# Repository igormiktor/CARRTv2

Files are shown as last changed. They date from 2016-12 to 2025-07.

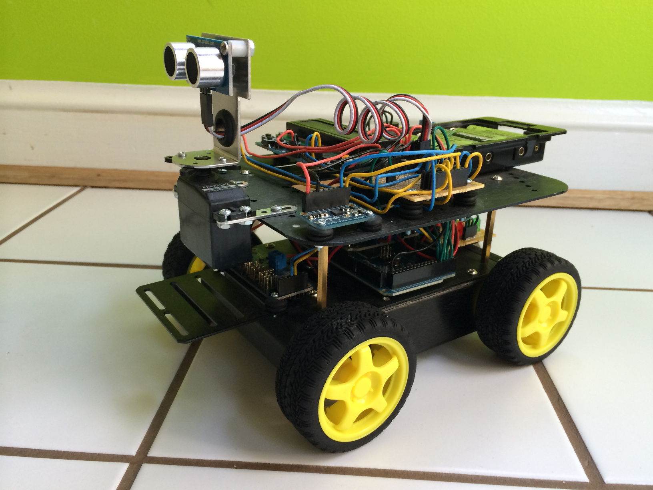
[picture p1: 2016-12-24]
images/CARRT_01.jpg

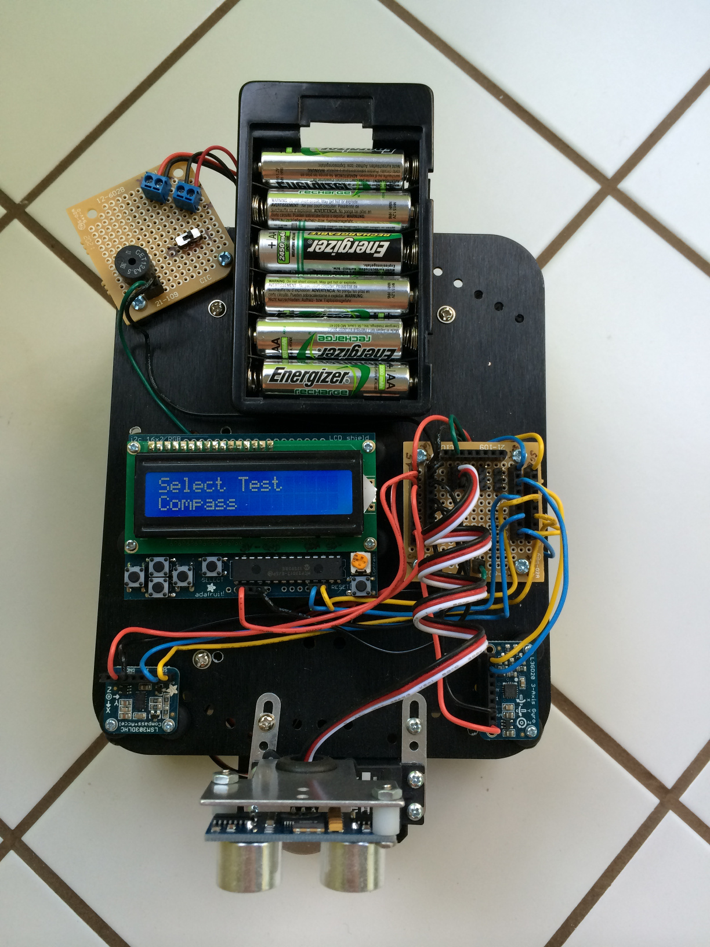
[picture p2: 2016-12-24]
images/CARRT_04.jpg

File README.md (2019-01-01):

# CARRTv2
Cute Autonomous Robot Rover Thing (version 2)

Goal of this project is to create a small robotic vehicle (CARRT) that can do the following:

- Start in one room of the house;
- Receive a goal position, specified relative to its starting location (e.g., 8 meters North, 4.5 meters West);
- Autonomously make its way to the new position, mapping doors and walls with its ultrasonic radar until it finds a path to the goal;
- Build a map as it goes, enabling effective back-tracking whenever it hits a dead-end.

This is both a hardware and a software project.

The hardware consists of a four-wheeled chassis carrying an ArduinoMega 256 and an Adafruit motor driver board.  Navigation is
enabled by an LSM303DLHC three-axis accelerometer and magnetometer and an L3GD20 three-axis gryoscope.  A Garmin Lidar Lite
sensor mounted on a servo allows CARRT to sense obstacles (both furniture and walls) and navigate around them.

The hardware and how it is wired together is described in the `schematics` sub-directory by a
[Fritzing](http://fritzing.org/home/) project file.
Photos of CARRT appear in the `images` sub-director and on the project wiki.

The software is found in the `source` directory.  Having the entire software
system fit and operate within the constraints of the ArduinoMega 256 (8 bit, 16
MHz ATmega 2560 microcontroller; 8 KB SRAM; 256 KB program memory) is the
primary challenge.  The rather low precision of the LSM303DLHC and the L3GD20 as
well as the poor reliability of a magnetometer operating inside a house (bring
up the compass on an iPhone, set the iPhone on the floor and just watch as you push
the iPhone slowly past an operating refrigerator) make indoor navigation the
secondary challenge.

The name "CARRT" is thanks to my daughter.

## Specs

* Main microcontroller
    * Arduino Mega256 board
    * CPU: ATmega2560 8-bit, 16MHz microcontroller
    * 256KB flash memory (program memory)
    * 8KB SRAM (working memory)
    * 4KB EEPROM (permanent memory)
* Power buses
    * Two power buses
    * First power bus supplies the Arduino Mega256
        * Arduino in turn supplies regulated 5V power to all other ICs
    * Second power bus supplies unregulated power to motors and servos
* Motor controllers
    * L293D H-Bridge ICs to control 4 DC motors
    * Total of 4 L293Ds are used
    * L293Ds control the unregulated motor power bus
    * L293Ds stacked in pairs to support 1.2A sustained current to DC motors
    * SN74H595 shift-register IC is used to control the L293Ds
    * SN74H595 works off the regulated 5V power bus
* 2 x 16 character LCD display
    * LCD controlled by an HD44780U
    * MCP23017 drives the HD44780U
* LSM303DLHC triple-axis accelerometer and magnetometer
* L3GD20 triple-axis gyroscope
* PCA9685 16-channel PWM/Servo driver
    * Used to drive the Parallax servo
* Parallax 900.00008 servo
* Garmin Lidar Lite v3
    * Mounted on the Parallax servo
* PING))) ultrasonic distance sensor
    * Used for obstacle detection while moving
* TMP36 analog temperature sensor
* PS1240 piezoelectric buzzer

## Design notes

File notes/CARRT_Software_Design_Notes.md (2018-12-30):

# CARRT Software Design Notes

## Design Principles

This version of the software is based on the following design principles:

1. **Highly modular and decoupled.** Compartment details as much as
possible; present only the higher level interfaces needed by other
components, and no more.

2. **Separate low-level hardware interfaces from higher-level code.** Software
drivers are provided for all the hardware sub-systems, even trivial hardware
such as the piezo-electric buzzer. In keeping with principle #1, all details of
the hardware are encapsulated by the drivers.

3. **Prefer functional interfaces to object interfaces.** All the
hardware on CARRT is "one of".  This is true even for the four drive
motors because they are all controlled through a single SN74H595 and so behave
as a single hardware subsystem.  If hardware drivers are presented as
objects, then the code has to manage a singleton object and make it
visible to code that needs to access it.  Functional interfaces are
easier and cleaner in this case, and avoid the proliferation of global
objects or the overhead of singleton classes to manage them.

4. **Use namespaces to compartmentalize modules.** Namespaces serve to
prevent name clashes and bind the functions that belong together
logically, much like using static class members. They also expose a
simplified interface in header files, as compared to classes with static members.

5. **Represent CARRT higher-level functions as an event-driven state
machine.**   Whatever CARRT is doing is represented as a state.
Changes in behavior are changes in state. States are narrowly
defined and simple.  More complex behaviors are decomposed into
simpler actions that correspond to simple, easily defined states.

6. **Represent states by classes.**  In this case, objects are the natural and
appropriate way to implement states.  Objects that inherit from a base class
allow simple and consistent management of states and a seamless process for
switching between states.

7. **States, and only states, are created dynamically.**  It may seem crazy
to use dynamic memory allocation on a microcontroller, but this principle is
based on actual testing that showed dynamic allocation offered the best
tradeoff.  If states are not allocated dynamically, then all states have to be
allocated globally, which consumes a very significant amount of SRAM (states are
generally small, but there are many of them).  Because only one state is active
at a time, and no more than two are ever "alive" simultaneously (when states are
changing, both the outgoing and incoming states are briefly alive at the same
time), allocating states dynamically offers a significant reduction in
memory used at any instant in time.  Further supporting the use of dynamic
memory allocation for states are the following considerations:
    * The avr-libc implementations of `malloc()` and `free()` (upon
    which `new` and `delete` are implemented) are efficient and
    relatively fast.  And `free()` is pretty good at minimizing heap
    fragmentation.
    * The pattern of how states are allocated and released (create a new
    state; delete the old one; repeat) combined with the generally small
    size of states limits the fragmentation of the heap to at most a
    free block the size of the largest state.  And even that fragment will be
    reclaimed on the very next state change because a new smaller state
    will then be created at the bottom of the heap (where the free
    fragment is) and then all the memory above it will be recombined
    into an un-fragmented free block when the old state (the state that
    had fragmented the heap) is released.

8. **Navigation is provided as a separate, stand-alone service.** The
Navigator is in essence a higher-level "driver" that is implemented on top of
the lower-level hardware drivers.

9. **All strings are placed in PROGMEM (flash memory).**  SRAM is
precious.  Because strings are needed only to support the user interface,
string operations are never time critical.  While putting strings
in PROGMEM makes access much slower, the slower access doesn't matter
and the reduced SRAM usage is really important.

10. **Support selective compilation of major elements.**  CARRT is constrained
by SRAM. While it is useful to have a full set of testing code, it invariably
uses up precious SRAM.  So it is important to build the code in a way that
testing code (or any other major elements of CARRT, such as the "programmed drive"
feature) can be omitted at compile time while still building a CARRT executable
that is otherwise fully operational apart from the omitted functionality

## History and Lessons

The initial implementation of CARRT software was developed in parallel with the
hardware build. There were many lesson learned on both sides. For example, the
original hardware had only a single power bus for both the motors and the
electronic components.  Initial testing showed this to be a bad design: when the
motors turned on they caused large voltage drops that then triggered a reset in
the ATmega 2560. That's why now there are two separate power buses, one for motors
and one for ICs. Another example is that trying to drive a servo directly from
the ATmega 2560 using PWM caused servo jitter due to the many other interrupts
that the ATmega 2560 had to service.  This is why CARRT now uses a dedicated PCA9685
board to control the servo.

The initial software also avoided use of dynamic memory allocation: all
states were pre-allocated as global objects.  As the number of states grew, this
quickly consumed much of available SRAM.  This was further exacerbated by
numerous user-interface strings that were stored in SRAM.  Each behavior (i.e.,
state) added to CARRT further exacerbated the problem.

Implementing software interfaces to hardware as objects created a
significant number of global objects that had to be managed and shared.
Eventually, this became a header file full of `extern` declarations of
global objects, which in turn had to include headers defining each of
these objects.  This became a headache to manage, slowed compilation,
and had the effect of making everything dependent on everything.

Additionally, some of the software interfaces were initially coded at the
wrong level of abstraction (generally too low a level).  This resulted in
what effectively became multiple layers of drivers (each somewhat higher
level) for a single (simple) piece of hardware.  This was needlessly
inefficient and hard to understand and debug.

Finally, the parallel development of hardware and software not only resulted in
a somewhat ad-hoc development of code, but also led to
undesirable coupling of testing code and operational code in some places and
code duplication in others.  This was inherently inefficient and as well as hard to
adapt and maintain when new hardware was added and/or changes were need.

All these lessons (and numerous smaller ones) have been incorporated
into version 2 of the CARRT software.

## Implementation Overview

The implementation is at its core an event-driven state machine: the heart of
CARRT is an event loop that takes incoming events, feeds them to the current
state, which in turn takes appropriate actions (including triggering a change to
a new state).

The top level view of current CARRT implementation is as
follows:

* Initialization.  Configure the microcontroller appropriately, initialize all
hardware subsystems, initialize the state machine, and start internal timers.

* Event loop. This is the heart of CARRT.  The main loop is very simple: pull
the next event from the event queue, handle any system-level events (navigation
updates, errors, resets, etc), pass any other events to the current state (this
is where all the behaviors happen), and then (when the state is done with the
event) optionally perform (non-essential) housekeeping tasks.

* Reset. If a reset is requested, ensure everything is shutdown appropriately,
clean up, and then go back to initialization.

Initialization and reset are handled in CarrtMain.cpp; the event loop is managed
in MainProcess.cpp.  State behavior is defined by the State class (State.h
and State.cpp).  States have a simple interface of three member functions:
onEntry(), onEvent(), and onExit().  When a state becomes active (i.e.,
current), but before any events are processed, MainProcess will call the state's
onEntry() function.  This provides a mechanism for the state to initialize or
otherwise prepare itself.  The MainProcess will then repeatedly pass events to
the state's onEvent() function.  It will continue to do so until there is a
change of state (usually, but not always, initiated by the current state's onEvent()
function).  When a change of state is triggered, the MainProcess will then call
the current (about to depart) state's onExit() function, allowing the state to perform whatever clean
up is appropriate.  In most cases, the last thing the state's onExit() will do
is delete itself: this is the default action of State::onExit(). In some
situations (e.g, for states that are part of a user-entered program of actions
which the user may replay repeatedly) states will override the self-delete
behavior in onExit().  After calling the departing State's onExit(), MainProcess will
then call the incoming State's onEntry() function.

Events are defined and managed by the EventManager (EventManager.h,
EventManager.cpp).  At this time, events consist of timer-related events,
navigation-related events, keypad-related events, and error events.  The
timer-related events are the most important, as they provide the heart-beat that
enables States to preform a variety of actions, such as monitoring drive
progress or navigation parameters, updating displays, tracking elapsed time, and
initiating time-related actions.  Timer-related events are generated by the
EventClock (EventClock.h and EventClock.cpp), which relies on one of the ATmega
2560's hardware timers to trigger interrupts that are used to queue
timer-events. Note also that changes of state are not events, but rather
something that happens as a result of an event.

The inertial navigator (Navigator.h and Navigator.cpp) is implemented as an
independent module that effectively runs in the background.  The MainProcess
feeds it dedicated navigation update events every eighth of a second, which the
Navigator uses to read accelerometer, magnetometer, and gyroscope data and update
its internal navigation state.  At any time, States can call appropriate
Navigator functions to obtain the current position, direction, and velocity.  To
help the Navigator out, States inform the Navigator about what CARRT is doing
(e.g., driving straight, turning, stopped, etc) by calling appropriate Navigator
functions (e.g., Navigator::movingStraight(), Navigator::movingTurning(),
Navigator::stopped(), etc).

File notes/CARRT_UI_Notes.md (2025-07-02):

# CARRT User Interface Overview

## Keypad
```
+-----------------------------------------+
| +-------------------------------------+ |
| |                 LCD                 | |
| +-------------------------------------+ |
|        1                                |
|     2     3    5   <--- Keypad Buttons  |
|        4                                |
+-----------------------------------------+
```

The diagram above identifies the buttons on the LCD keypad.  These are
referred to as follows:

* button 1 = UP
* button 2 = LEFT
* button 3 = RIGHT
* button 4 = DOWN
* button 5 = SELECT

It is also possible to enter simultaneous combinations of buttons, referred to as "chords".
Several chords have unchanging meaning.  These chords are:

* button 3 & button 5 = RIGHT & SELECT = RESET
* button 2 & button 3 = LEFT & RIGHT  = PAUSE
* button 1 & button 4 = UP & DOWN     = CONTINUE

* RESET always performs a full soft reset of CARRT.  All systems and sub-systems are
completely reinitialized.  It is effectively equivalent to cycling the power.

* PAUSE suspends the current activity in the sense that no further
state-level event processing (and therefore no further state-level
actions) will occur.  Note that "pause" can in some cases be
counterintuitive:  pausing a "forward drive" state while it is driving
will effectively cause CARRT to continue to drive indefinitely: the
events that trigger driving to stop will not be processed.

* CONTINUE will "undo" a PAUSE, allowing the active state to continue
processing events and taking corresponding action.  Note that "continue"
can in some cases be counterintuitive:  continuing a paused "forward
drive" state while it is driving will may not cause it to stop: if the
events that trigger driving to stop have already gone by, then the state
will never see them and will therefore not stop.

Apart from the above chords, the meaning of the buttons varies with menu items,
although the operation is generally intuitive.  The precise meanings, especially
any that are not perhaps intuitive, are described in the appropriate menu
sections.

## Menus

The menu system has a consistent user interface:  the UP and RIGHT buttons move
to the next menu item; the DOWN and LEFT buttons move to the previous menu item;
the SELECT button selects that menu item.

The remaining sub-sections walk through the menu options

### Welcome to CARRT (top-level menu)

This is the top-most menu in CARRT.  It presents four menu options:

* **Run Tests...** Leads to a menu of test options.

* **Prgm Drive...** Leads to menus that allow users to program a drive and run
it.

* **GoTo Drive...** Leads to menus that allow users to enter a destination and
have CARRT go to it.

* **Nav Info...** Displays CARRT's current position (relative to the
original starting position) and the current heading.

* **About...** Leads to menus that display information about CARRT's firmware.

Note that the first three options are present only if they are selected at
compile time.

### Run Tests... (second-level menu)

This menu presents a series of tests.  Selecting one of them runs the corresponding test.
The options under this menu are:

* **Exit...**  Returns to the top-level menu

* **Memory** Displays memory information.  The UP and DOWN buttons toggle
between displaying total free SRAM and total used SRAM. The LEFT and RIGHT
buttons toggle between displaying total SRAM and displaying the SRAM between the
stack and the heap (the "free stack" space).  The SELECT button returns to the **Run
Tests...** menu.

* **1/4 Sec Events**  Counts 1/4 second events.  Continues until any button is
pressed, which returns to the **Run Tests...** menu.

* **1 Sec Events**  Counts 1 second events.  Continues until any button is
pressed, which returns to the **Run Tests...** menu.

* **8 Sec Events**  Counts 8 second events.  Continues until any button is
pressed, which returns to the **Run Tests...** menu.

* **Beep**  Makes beep sounds until any button is pressed, which returns to the
**Run Tests...** menu.

* **Temp Sensor**  Displays the temperature as measured by the TMP36 analog
temperature sensor, updated every second.  Pressing any of the UP, DOWN, LEFT,
or RIGHT buttons toggles the display between degrees F and C.    The SELECT
button returns to the **Run Tests...** menu.

* **Batt LEDs**  Cycles through the battery level LEDs.  Continues until any
button is pressed, which returns to the **Run Tests...** menu.

* **Motor Batt**  Displays the voltage of the batteries that power the motors
and servos, updated every second.    Continues until any button is pressed,
which returns to the **Run Tests...** menu.

* **CPU Batt**    Displays the voltage of the batteries that power the electronic
components, updated every second.    Continues until any button is pressed,
which returns to the **Run Tests...** menu.

* **Sonar**  One a second the sonar measures and displays the range to whatever
is in front of it.  Continues until any button is pressed, which returns to the
**Run Tests...** menu.

* **Lidar**  The lidar slews to straight ahead, makes a range measurement, and
displays it.  Pressing the LEFT or RIGHT buttons slews the lidar accordingly.
Pressing the UP or DOWN button triggers a new lidar range measurement at the
current slew angle.  The SELECT button returns to the **Run Tests...** menu..

* **Range Scan**  The lidar performs a scan from right to left (covering a 120
degree arc), measuring and displaying the range to the nearest obstacle at 10
degree increments.  Every 4 seconds, the lidar slews 10 degrees to the new
bearing angle and displays the range to the nearest obstacle.  Continues until
any button is pressed, which returns to the **Run Tests...** menu.

* **Compass**  Displays the compass bearing in degrees, updated every
second.  Continues until any button is pressed, which returns to the
**Run Tests...** menu.

* **Accelerometer**  Displays the accelerometer readings in Gs, updated every
second.  The LEFT and RIGHT buttons cycle the display through the x-, y-, and
z-axes.  The UP and DOWN buttons toggle the display between raw accelerometer
readings and nulled accelerometer readings (nulled means the average at-rest
accelerometer reading is subtracted out).  The intent is that you can observe
the readings as CARRT is manually moved around.  The SELECT button returns to
the **Run Tests...** menu.

* **Gyroscope**  Displays the gyroscope readings in deg/sec, updated every
second.  The LEFT and RIGHT buttons cycle the display through the x-, y-, and
z-axes. The UP and DOWN buttons toggle the display between raw gyroscope
readings and nulled gyroscope readings (nulled means the average at-rest
gyroscope reading is subtracted out).  The intent is that you can observe the
readings as CARRT is manually spun around.  The SELECT button returns to the
**Run Tests...** menu.

* **Drive Fwd/Rev**  Repeatedly drives forward for a second, pauses for a
second, drives backward for a second, and pauses for a second.  Continues until
any button is pressed, which returns to the **Run Tests...** menu.

* **Drive Left/Right**  Repeatedly rotates left for a second, pauses for a
second, rotates right for a second, and pauses for a second.  Continues until
any button is pressed, which returns to the **Run Tests...** menu.

* **Nav. Rotation**  Engages the Navigator and displays which direction CARRT
believes it is pointed in (according to both compass and Navigator), updated
every second.  Continues until any button is pressed, which returns to
the **Run Tests...** menu.  The intent is that CARRT will be place on a
lazy-susan and spun around to check the performance of the Navigator.

* **Nav. Drive**  Engages the Navigator, drives forward for 5 seconds, and then
pauses to display how far (in cm) CARRT's Navigator believes it has traveled from
its starting point.  When any of the LEFT, RIGHT, UP, or DOWN buttons is pressed,
CARRT drives in reverse for 5 seconds, and again pauses to display how far CARRT's
Navigator thinks it is from its original starting point.  This continues until the
SELECT button returns to the **Run Tests...** menu. This allows checking CARRT's
internal estimates of distance traveled against actual measurements.

* **Error Handling**  Displays a short count-down and then triggers a error
condition, which (should) lead to the display of an error message (error code
601). The only recovery options are to perform a soft reset by simultaneously pressing
the RIGHT and SELECT buttons, or cycling the power.

### Prgm Drive... (second-level menu)

This set of menus allows the user to select from a set of actions and add them
to list of programmed CARRT actions.  Users can also clear the list or run the
list of actions (a "programmed drive").  The list is remembered (even if the
user exits the **Prgm Drive...** menu) until it is explicitly cleared.  The
number on the right
side of the top-row of the LED display shows the number of actions in the
currently stored "programmed drive".

The options under this menu are:

* **Exit...**  Returns to the top-level menu (the list of actions is
remembered).

* **Go Fwd Time**  Go forward for a user-specified number of seconds.

* **Go Fwd Dist**  Go forward for a user-specified distance in cm.

* **Go Rev Time**  Go in reverse for a user-specified number of seconds.

* **Go Rev Dist**  Go in reverse for a user-specified distance in cm.

* **Rotate L Time**  Rotate left (counter-clockwise) for a user-specified number
of seconds.

* **Rotate R Time**  Rotate right (clockwise) for a user-specified number of
seconds.

* **Rotate Angle**  Rotate a user-specified angle in degrees.  Negative angles
are to the right (clockwise); positive angles are to the left
(counter-clockwise).

* **Pause**  Pause (do nothing) for a user-specified number of seconds.

* **Beep**  Beep for a user-specified number of seconds.

* **Scan**  Conduct a range scan from -60 degrees relative to 60 degrees
relative, measuring and displaying the range to the nearest obstacle every 10
degrees.

* **Run it...**  Run the "programmed drive" using the currently stored actions.

* **Clear...**  Erase the currently stored actions.

### GoTo Drive... (second-level menu)

This set of menus allows the user to set a Go-To point and have CARRT
then autonomously drive to that Go-To point.  The Go-To point can be entered
either relative to CARRT's current orientation and position or in absolute
North and East coordinates measured from CARRT's current position.

The options under this menu are:

* **Relative Goto...**  Specify a Go-To point relative to CARRT's current
orientation and position.  A series of prompts will allow the user to enter
the Go-To point as cross-range and down-range in centimeters (cm) from CARRT.
Forward (downrange) and left/counter-clockwise (crossrange) are positive;
backward and right/clockwise are negative.

* **N & W Goto...**  Specify a Go-To point in North and West coordinates
measured from CARRT's current position.  A series of prompts will allow the
user to enter the Go-To point as distance (cm) to the North and West of CARRT.
South and East are entered as negative values.

* **Exit...**  Returns to the top-level menu.

### Nav Info... (second-level menu)

This menu displays the current position in centimeters North and West of the
original starting position, as well as the current heading (direction CARRT
is pointed towards) in degrees.  This is static information that is not
updated if CARRT is manually moved while the information displays.

Pressing any button returns to the top-level menu.

### About... (second-level menu)

This menu displays a series of information about CARRT's current firmware. The
UP and RIGHT buttons move to the next display; the DOWN and LEFT buttons move
to the previous display.  The SELECT button returns to the top-level menu.
The display options are:

* **Version**  Displays the version number of the software and the features
included in the firmware.  The feature codes are:
    * **T**  Firmware includes Tests
    * **P**  Firmware includes Programmed Drive
    * **G**  Firmware includes GoTo Drive
    * **IMU**  Firmware uses inertial navigation
    * **DR**  Firmware uses dead-reckoning navigation
    * **D**  Firmware includes debugging output using Serial0

* **Build Date**  Displays the date and time the firmware was built.

* **Git SHA1**  Displays the SHA1 of the git HEAD from which the firmware was
built. This is useful for recreating the exact firmware currently loaded on
CARRT.

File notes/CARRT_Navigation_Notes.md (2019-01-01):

# CARRT Navigation Notes

## Overview

CARRT can be compiled with one of two different navigation modes. The first mode
is inertial navigation. It uses the accelerometer, magnetometer and gyroscope as
an inertial measurement unit, estimating distance moved by (double)
integration of the acceleration.  The second mode is dead reckoning.  This mode
uses the accelerometer, magnetometer, and gyroscope for orientation only,
and estimates distance moved using an empirically-derived formula that
converts time spent moving into distance moved.  The mode is chosen at compile time by
#defining either CARRT_NAVIGATE_USING_INERTIAL or
CARRT_NAVIGATE_USING_DEADRECKONING.

## Common to both Navigation Modes

The overall approach to navigation, the underlying choices of coordinate systems, and the implementation of
these fundamental elements are common to both navigation modes.  These common elements are:

* Coordinate system: The global coordinate system used by CARRT for navigation places North along the
positive X-axis and West along the positive Y-axis.  This allows the 0 direction to map to North and
enables the standard conversions between Cartesian (x,y) coordinates and Polar (r,&theta;) coordinates.
All navigation and navigation-related activities, such as mapping, are done in the global (N,W) coordinate
system.

* Local coordinates: The accelerometer and magnetometer both provide data in local, CARRT-centric,
3-D coordinates in which the X-axis points in CARRT's forward direction, the Y-axis points
to CARRT's left, and the Z-axis points upward.  The gyroscope provides angular rates along these same
three local axes. The conversion from local coordinates to global coordinates is dynamic, changing
over time as CARRT's orientation in 3-space changes (of course, orientation in the horizontal plane is
the primary consideration because CARRT usually doesn't drive on slopes&mdash;but the conversion
also works in that case).

* Angles: Navigation internally uses standard mathematical angles in radians, measured counter-clockwise
from the X-axis (North-axis). Conversion to compass angles is straightforward:

    compass = (360 - &theta; * 180 / pi) modulo 360

* Units: The units for the global (N,W) coordinates are internally maintained in meters (m).  Velocity is in
m/s, and acceleration is in m/s^2.  For convenience, centimeters (cm) units are commonly used in displays and
for keypad entry.

* Update rate: Navigation parameters are updated every 1/8 second.  The update reads all three instruments
(accelerometer, magnetometer, and gyroscope) and updates the orientation and position of CARRT.

Both navigation modes execute the following overall process:

1. Read the accelerometer, magnetometer, and gyroscope.

2. Estimate CARRT's current compass heading from the accelerometer and magnetometer data.  This step
also establishes the coordinate transformation between the local and global coordinate systems.

3. Estimate CARRT's current compass heading by integrating the gyroscope's angular rate data.

4. Combine the two compass estimates to get a "best" estimate for CARRT's current compass heading.

5. Using a velocity estimate (obtained differently for the different navigation modes), estimate
the distance traveled and update the global (N,W) coordinates of CARRT's current position.

The coordinate transformation figured out in step 2 is essential to all other
computations because all measurement data is in 3-D local coordinates but
must ultimately be converted to the 2-D global (N,W)
coordinate system. It isn't immediately obvious how to get to the global
coordinate system from the accelerometer, magnetometer, and gyroscope
measurements which are reported  as 3-D vectors in local coordinates.  The key to
converting from local to global coordinates is the observation that the cross
product of the magnetometer and the accelerometer output vectors gives an East
vector expressed in local coordinates.  The magnetometer output is a North
vector expressed in local coordinates, and these two vectors (East and North)
provide an orthogonal basis vector set for the global coordinate system expressed
in local coordinates.  With this basis set in hand, the local-to-global conversion
is straightforward.

## Inertial Navigation Mode

In inertial navigation mode the first 4 steps are executed as described above.
To implement step 5, the acceleration vector from the accelerometer is first
converted from local to global (N,W) coordinates. It is then integrated and
added to the velocity from the prior time-step to produce an estimate of the
current velocity vector.  A second integration is then performed on the current
velocity to get distance traveled and the result is added the position at the
prior time-step.  This generates an estimate of CARRT's current position.

The double integration required in inertial navigation mode is very sensitive
to errors in the acceleration measurement.  Several mechanism are used to help
limit those errors:

* To obtain the best acceleration measurement possible, each accelerometer "measurement" actually is an
average of 12 accelerometer measurements equally spaced in time over the previous 1/8 second.

* The measured acceleration is filtered to remove near-zero values. These small, near-zero accelerations are
replaced by 0 to ensure that "noise" isn't treated as actual acceleration (which if repeatedly integrated
can generate significant velocities).  The filter settings were determined empirically by analyzing the
noise in accelerometer measurements while CARRT was stationary.

* The estimated velocity obtained after integrating acceleration is constrained to what has been empirically
determined as CARRT's top speed.  This prevents the integration process from producing unreasonable velocities.

* When CARRT stops, velocity and acceleration are forced to 0 (regardless of what the accelerometer or other
instruments report).  And no navigation updates occur while CARRT is stopped.

Despite these steps, the velocity estimates occasionally spike high, maxing out velocity and excessively
over-estimating the distance traveled.  However, in most cases inertial navigation mode tends to underestimate
distance traveled.  The underestimate is generally 40% to 70% of actual distance traveled. The amount
underestimated cannot be reliably reproduced and seems to have a random component.  I have not been able to
determine the cause of these underestimates.  Nor, for that matter, have I been able to determine the cause of
the occasional velocity spikes.

For these reasons, I implemented an alternate navigation mode that implements dead-reckoning.

## Dead-Reckoning Navigation Mode

The implementation of dead-reckoning navigation mode follows the same first 4 steps, just like inertial
navigation mode.  This includes taking accelerometer measurements because the acceleration vector is needed
to compute heading and determine the conversion from local to global coordinates.  In dead-reckoning mode,
this is the only use of  acceleration data.

To compute distance traveled, dead-reckoning mode uses a simple linear model of distance traveled as a
function of time.  This model was derived from empirical measurements of how far CARRT traveled over time. The
data showed that a linear model was a surprisingly good fit. This linear model is documented and implemented
in DriveParam.cpp, which includes functions to compute both distance given time and time given distance.

So, at each 1/8 second update,  dead-reckoning navigation mode simply uses the linear model to
compute how far CARRT traveled during that 1/8 of a second and applies it along CARRT's current heading
vector to update the prior time-step position to the current position.

Dead-reckoning mode has some risks and error sources:

* Doesn't account for slippage or slowing due to obstacles (e.g., getting over the lip of a rug).

* Doesn't account for drive speed dropping as motor battery levels drop. However, limited experimentation
indicates that CARRT drive speed stays pretty constant until some point at which it drops significantly and
rapidly.  So this problem can be minimized by driving with batteries that are "not too low".

* The linear approximation error is highest for short (< ~2 sec) drives.  But even then the error in the linear
model is much less than the errors observed from inertial mode navigation.  Note that this applies to actual
drive times&mdash;not 1/8 second intervals of a longer drive.  Because of the linear model, adding up 1/8 second
intervals to compute distance traveled during a 30-second drive produces the same answer as computing the
distance traveled for a 30-second drive. The statement here applies to an actual drive: the estimate for a 30-second
drive (regardless of how it is computed) will be pretty accurate; the estimate for a 1/2 second drive (however computed)
will be much less accurate.

All-in-all, the dead-reckoning navigation model appears to work well enough for autonomous driving over the kinds
of distances and conditions encountered during "inside the house" driving that CARRT was designed for.

Nevertheless, it is frustrating that I couldn't get inertial navigation mode to work...

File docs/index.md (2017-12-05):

---
layout: home
#title: CARRT &mdash; an Autonomous Path-Finding Rover
#permalink: /
---

# CARRT v2

Goal of this project is to create a small robotic vehicle (CARRT) that can do the following:

- Start in one room of a house;
- Receive a goal position relative to its current position;
- Autonomously make its way to the goal position, mapping doors and walls with its lidar until it finds a path to the goal;
- Build a map as it goes, enabling effective back-tracking whenever it hits a dead-end.

And do it all based on an 8 bit, 16 MHz microcontroller with only 8 KB of SRAM...

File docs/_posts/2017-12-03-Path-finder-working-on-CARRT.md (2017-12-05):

---
layout: post
title:  "Pathfinder working on CARRT"
date:   2017-12-03 10:09:18 -0500
categories: CARRT update pathfinder
---

The pathfinder is now implemented and tested on CARRT itself.  The original pathfinding code was developed and tested on Linux.
It's now working on CARRT's 8-bit, AVR processor with only 8K of SRAM.

It's been tested both with "manually" entered maps (PathFindingBasicTest.cpp) and with lidar-generated maps (PathFindingTest.cpp).

Next task is to create the menus and states that actually execute the pathfinding and then drive the resulting path (re-mapping and
re-pathfinding as appropriate along the way).

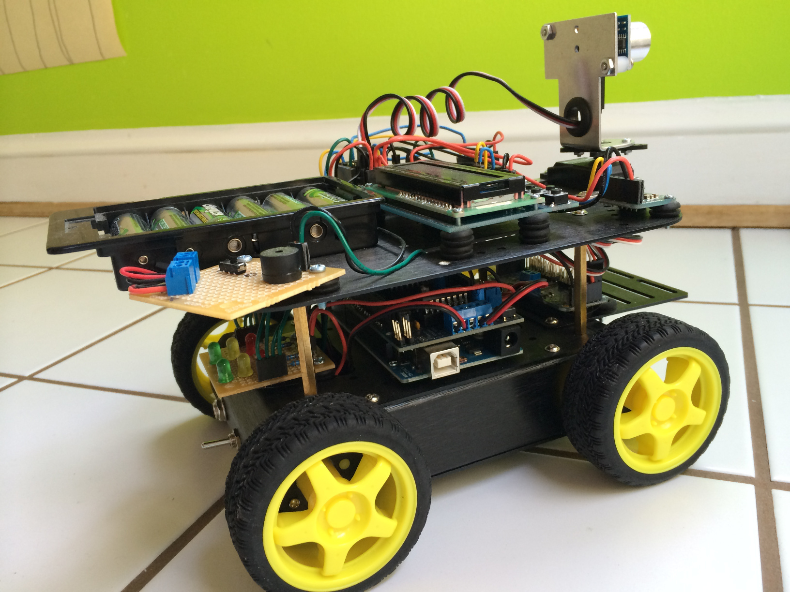
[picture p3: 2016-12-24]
images/CARRT_03.jpg

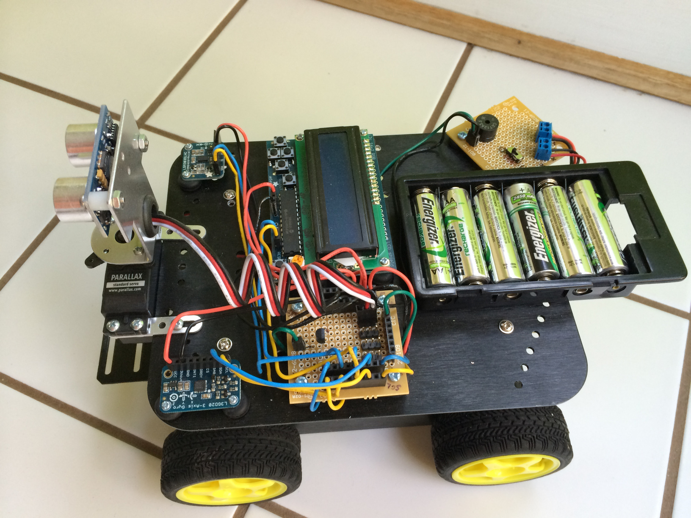
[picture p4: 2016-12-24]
images/CARRT_02.jpg

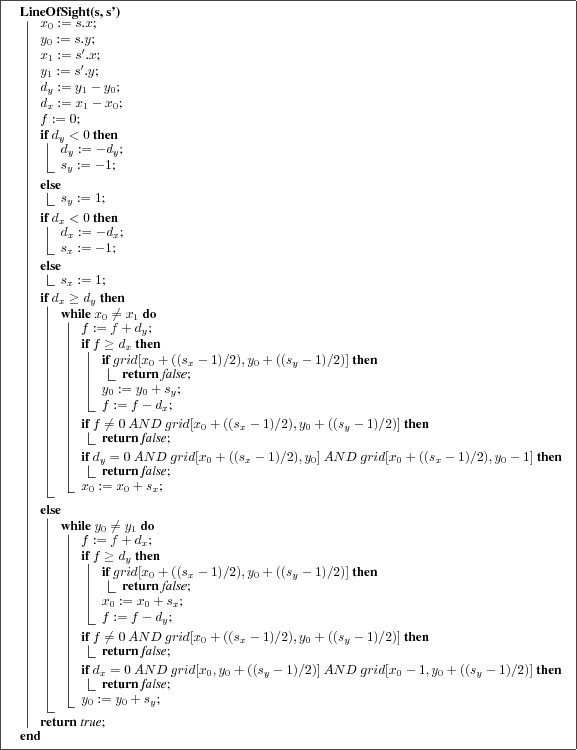
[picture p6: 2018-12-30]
notes/LoS.png

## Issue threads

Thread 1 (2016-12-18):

To do list

igormiktor, 2016-12-18:
Testing checklists

- [ ] Display driver
- [ ] Keyboard driver
- [ ] Navigator
- [ ] Map Keeper

igormiktor, 2017-01-07:
Notes fixes:

- [ ] Reset is right & select
- [ ] Four too level menu options
- [ ] The options are....
- [ ] free stack space
- [ ] covering a 120 degree arc
- [ ] compass updates every second
- [ ] intent of nav drive

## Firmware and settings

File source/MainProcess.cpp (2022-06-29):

/*
    MainProcess.cpp - Functions that run CARRT's main process which manages
    CARRT's states

    Copyright (c) 2022 Igor Mikolic-Torreira.  All right reserved.

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
    You should have received a copy of the GNU General Public License
    along with this program.  If not, see <http://www.gnu.org/licenses/>.
*/




#include "MainProcess.h"

#include "AVRTools/SystemClock.h"
#include "AVRTools/MemUtils.h"

#include "ErrorCodes.h"
#include "ErrorState.h"
#include "EventManager.h"
#include "Navigator.h"
#include "State.h"
#include "WelcomeMenuStates.h"

#include "Drivers/Battery.h"
#include "Drivers/Keypad.h"
#include "Drivers/Motors.h"

#include "Utils/DebuggingMacros.h"


#if CARRT_ENABLE_DEBUG_SERIAL

#include "BuildInfo.h"

namespace
{
    const unsigned int kMega2560SRam = 8192;

    const PROGMEM char sVersion[]       = CARRT_VERSION;
    const PROGMEM char sBuildDate[]     = CARRT_BUILD_DATE;
};

#endif


#ifndef CARRT_MIN_MEMORY
#define CARRT_MIN_MEMORY        64      // bytes
#endif




// Expand the namespace with some additional functionality private to this module

namespace MainProcess
{
    void checkForErrors();
    void processEvent();
    bool checkForUserInputs();
    void prepReset();
    bool handleRequiredSystemEvents( uint8_t event, int parameter );
    void handleOptionalSystemEvents( uint8_t event, int parameter );

    State*          mState;
    ErrorState*     mErrorState;
    bool            mNotPaused;
};






void MainProcess::init( ErrorState* errorState )
{
    EventManager::reset();

    mNotPaused = true;

    // Error state is special -- we hold it here for the duration
    // Low on memory is one of the error states, so we don't want to have to create
    // an error state on the fly
    mErrorState = errorState;

    mState = new WelcomeState;

    if ( !mState )
    {
        mErrorState->setErrorCode( kOutOfMemoryError );
        mState = mErrorState;
    }

    mState->onEntry();
}




void MainProcess::runEventLoop()
{
    DEBUG_PRINTLN_P( PSTR( "Version " CARRT_VERSION "  " CARRT_FEATURES ) );

    DEBUG_PRINT_P( PSTR( "Build " CARRT_GIT_HEAD_SHA1 " " ) );
    DEBUG_PRINT_P( sBuildDate );
    DEBUG_PRINTLN_P( PSTR( " " CARRT_BUILD_TIME ) );

    DEBUG_PRINT_P( PSTR( "Motor Batt mV = " ) );
    DEBUG_PRINTLN( Battery::getMotorBatteryMilliVoltage() );
    DEBUG_PRINT_P( PSTR( "CPU Batt mV = " ) );
    DEBUG_PRINTLN( Battery::getCpuBatteryMilliVoltage() );

    DEBUG_PRINT_P( PSTR( "SRAM Free (bytes) = " ) );
    DEBUG_PRINTLN( MemUtils::freeSRAM() );
    DEBUG_PRINT_P( PSTR( "SRAM Used (bytes) = " ) );
    DEBUG_PRINTLN( kMega2560SRam - MemUtils::freeSRAM() );
    DEBUG_PRINT_P( PSTR( "Stack Free (bytes) = " ) );
    DEBUG_PRINTLN( MemUtils::freeMemoryBetweenHeapAndStack() );

    while ( 1 )
    {
        checkForErrors();
        processEvent();
        if ( checkForUserInputs() )
        {
            // Reset triggered -- get out of the event loop
            break;
        }
    }
}




bool MainProcess::checkForUserInputs()
{
    const int kMinTimeBetweenButtonChecks = 250;        // milliseconds

    static unsigned long sNextTimeButtonClickAccepted = 0;

    uint8_t buttonHit = Keypad::readButtons();

    if ( buttonHit && millis() > sNextTimeButtonClickAccepted )
    {
        // Reset requested
        if ( buttonHit == Keypad::kChord_Reset )
        {
            prepReset();

            // Make sure we accept button clicks next time around
            sNextTimeButtonClickAccepted = 0;
            return true;
        }

        // Pause requested
        if ( buttonHit == Keypad::kChord_Pause )
        {
            // Set paused flag (we simply don't pass any events to the state when paused)
            mNotPaused = false;
            return false;
        }

        // Continue requested
        if ( buttonHit == Keypad::kChord_Continue )
        {
            // Clear paused flag
            mNotPaused = true;
            return false;
        }

        EventManager::queueEvent( EventManager::kKeypadButtonHitEvent, buttonHit );

        // Rollover happens in about 50 days, so don't worry about it
        sNextTimeButtonClickAccepted = millis() + kMinTimeBetweenButtonChecks;
    }

    return false;
}




void MainProcess::prepReset()
{
    // Give the state a chance to delete itself
    mState->onExit();
    mState = 0;

    // Make sure motors are off
    Motors::stop();
}




void MainProcess::processEvent()
{
    uint8_t eventCode;
    int16_t eventParam;

    if ( EventManager::getNextEvent( &eventCode, &eventParam ) )
    {
        // We have an event to process -- start with required system events
        if ( handleRequiredSystemEvents( eventCode, eventParam ) )
        {
            //  If returned true, (and not paused) give the current state a chance at the event
            if ( mNotPaused && mState->onEvent( eventCode, eventParam ) )
            {
                // If the state returned true, pass the event back to the system
                handleOptionalSystemEvents( eventCode, eventParam );
            }
        }
    }
}




void MainProcess::checkForErrors()
{
    if ( MemUtils::freeMemoryBetweenHeapAndStack() < CARRT_MIN_MEMORY )
    {
        setErrorState( kOutOfMemoryError );
    }
    else if ( EventManager::hasEventQueueOverflowed() )
    {
        setErrorState( kEventQueueOverflowError );
    }
}




void MainProcess::yieldMilliseconds( uint16_t millisecs )
{
    // Allows other event processing to occur while we pause for a while

    // Does NOT process state events (so safe to call from inside a state)

    uint8_t eventCode;
    int16_t eventParam;

    // No rollover problem for many days...
    unsigned long endTime = millis() + millisecs;

    while ( millis() < endTime )
    {
        if ( EventManager::getNextEvent( &eventCode, &eventParam ) )
        {
            // We have an event to process -- start with required system events
            if ( handleRequiredSystemEvents( eventCode, eventParam ) )
            {
                //  If returned true, give the optional system handlers a chance at the event
                handleOptionalSystemEvents( eventCode, eventParam );
            }
        }
    }
}




void MainProcess::changeState( State* newState )
{
    if ( !newState )
    {
        mErrorState->setErrorCode( kNullStateToChangeState );
        newState = mErrorState;
    }

    // Only change if there really is a change
    if ( newState != mState )
    {
        // Design relies on states to delete themselves (if appropriate)
        mState->onExit();
        mState = newState;
        mState->onEntry();
    }
}




bool MainProcess::handleRequiredSystemEvents( uint8_t eventCode, int eventParam )
{
    if ( eventCode == EventManager::kNavUpdateEvent )
    {
        Navigator::doNavUpdate();
        return false;
    }

    if ( eventCode == EventManager::kNavDriftCorrectionEvent )
    {
        // gNavigator.doDriftCorrection();
        return false;
    }

    if ( eventCode == EventManager::kErrorEvent )
    {
        setErrorState( eventParam );
        return false;
    }

    return true;
}




void MainProcess::handleOptionalSystemEvents( uint8_t eventCode, int parameter )
{
    if ( eventCode == EventManager::kEightSecondTimerEvent )
    {
        int batteryStatus = Battery::checkAndDisplayBatteryStatus();
        if ( batteryStatus != Battery::kBatteriesOkay )
        {
//          postErrorEvent( (batteryStatus == kMotorBatteryCriticalLow ? kMotorBatteryLowError : kCpuBatteryLowError ) );
        }
    }
}




void MainProcess::postErrorEvent( int errorCode )
{
    EventManager::queueEvent( EventManager::kErrorEvent, errorCode, EventManager::kHighPriority );
}




void MainProcess::setErrorState( int errorCode )
{
    mErrorState->setErrorCode( errorCode );
    changeState( mErrorState );
}




State* MainProcess::getErrorState( int errorCode )
{
    if ( errorCode )
    {
        mErrorState->setErrorCode( errorCode );
    }

    return mErrorState;
}

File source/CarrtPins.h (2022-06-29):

/*
    CarrtPins.h - Defines the ArduinoMega2560 pins used by CARRT

    Copyright (c) 2022 Igor Mikolic-Torreira.  All right reserved.

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
    You should have received a copy of the GNU General Public License
    along with this program.  If not, see <http://www.gnu.org/licenses/>.
*/



#ifndef CarrtPins_h
#define CarrtPins_h

#include "AVRTools/ArduinoMegaPins.h"


// *** Macro definitions to facilitate direct access to AVR pins


// Analog pins
#define pBatteryMotorVoltagePin             pPinA00     // Arduino pin A0, PF0 ( ADC0 )
#define pBatteryElectronicsVoltagePin       pPinA01     // Arduino pin A1, PF1 ( ADC1 )
#define pTemperatureSensorPin               pPinA02     // Arduino pin A2, PF2 ( ADC2 )

// Digital pins
#define pNotUsedInterruptPin                pPin02      // Arduino pin 02, PE4 ( OC3B/INT4 )

#define pBeepPin                            pPin13      // Arduino pin 13, PB7 ( OC0A/OC1C/PCINT7 )

#define pBatteryMotorLedGreenPin            pPin22      // Arduino pin 22, PA0 ( AD0 )
#define pBatteryMotorLedYellowPin           pPin24      // Arduino pin 24, PA2 ( AD2 )
#define pBatteryMotorLedRedPin              pPin26      // Arduino pin 26, PA4 ( AD4 )

#define pBatteryElectronicsLedGreenPin      pPin23      // Arduino pin 23, PA1 ( AD1 )
#define pBatteryElectronicsLedYellowPin     pPin25      // Arduino pin 25, PA3 ( AD3 )
#define pBatteryElectronicsLedRedPin        pPin27      // Arduino pin 27, PA5 ( AD5 )

#define pBatteryMotorChargerConnectedPin    pPin28      // Arduino pin 28, PA6 ( AD6 )

#define pRangeSensorDataPin                 pPin29      // Arduino pin 29, PA7 ( AD7 )

// Motor control pins
#define pMotorLatchPin                      pPin12      // Arduino pin 12, PB6 ( OC1B/PCINT6 )
#define pMotorClockPin                      pPin04      // Arduino pin 04, PG5 ( OC0B )
#define pMotorEnablePin                     pPin07      // Arduino pin 07, PH4 ( OC4B )
#define pMotorDataPin                       pPin08      // Arduino pin 08, PH5 ( OC4C )

#define pFrontRightMotorSpeedPin            pPin03      // Arduino pin 03, PE5 ( INT5/OC3C )
#define pRearRightMotorSpeedPin             pPin11      // Arduino pin 11, PB5 ( OC1A/PCINT5 )
#define pFrontLeftMotorSpeedPin             pPin06      // Arduino pin 06, PH3 ( OC4A/PCINT8 )
#define pRearLeftMotorSpeedPin              pPin05      // Arduino pin 05, PE3 ( AIN1/OC3A )



#endif

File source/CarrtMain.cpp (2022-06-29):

/*
    CarrtMain.cpp - CARRT's main function.  Initializes and hands off to
    the Main Process.

    Copyright (c) 2022 Igor Mikolic-Torreira.  All right reserved.

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
    You should have received a copy of the GNU General Public License
    along with this program.  If not, see <http://www.gnu.org/licenses/>.
*/




#include <avr/pgmspace.h>

#include "AVRTools/Analog2Digital.h"
#include "AVRTools/I2cMaster.h"
#include "AVRTools/InitSystem.h"
#include "AVRTools/MemUtils.h"
#include "AVRTools/SystemClock.h"

#include "DriveProgram.h"
#include "ErrorState.h"
#include "EventClock.h"
#include "MainProcess.h"
#include "Navigator.h"

#include "Drivers/Battery.h"
#include "Drivers/Beep.h"
#include "Drivers/Display.h"
#include "Drivers/L3GD20.h"
#include "Drivers/Lidar.h"
#include "Drivers/LSM303DLHC.h"
#include "Drivers/Motors.h"

#include "Utils/DebuggingMacros.h"




namespace
{

    void doInitialization();
    void initializeCPU();
    void initializeNetwork();
    void initializeDevices();
    void initializeNavigator();
    void doResetActions();

    const PROGMEM char sMsgCarrtIs[]            = "CARRT is";
    const PROGMEM char sMsgCarrtImuIs[]         = "CARRT Nav is";
    const PROGMEM char sMsgInitializing[]       = "Initializing...";
};




int main()
{
    // Run/Reset loop
    while ( 1 )
    {
        // Initialize all the various subsystems
        doInitialization();

        // Create the error state (so we don't have to create it when out of memory; reused throughout)
        ErrorState errorState;
        MainProcess::init( &errorState );

        // Beep again to indicate ready to go
        Beep::readyChime();

        // Start the CARRT's internal clock (different from system clock)
        EventClock::init();

        // Everything important happens here...  Only ever return on a reset
        MainProcess::runEventLoop();

        // Only get here if resetting...
        doResetActions();
    }
}



namespace
{

    void doInitialization()
    {
        initializeCPU();

        // Beep to announce we are spinning up
        Beep::initBeep();

        // Allow some time for capacitors to charge
        delayMilliseconds( 500 );

        initializeNetwork();
        initializeDevices();

        DEBUG_INIT_SERIAL_OUTPUT();
#if CARRT_ENABLE_DEBUG_SERIAL
        Display::displayBottomRowP16( PSTR( "Debug Enabled" ) );
#endif

        // Allow any 'power on' vibrations to dampen out before
        // starting inertial measurement unit
        delayMilliseconds( 2000 );
        initializeNavigator();

#if CARRT_INCLUDE_PROGDRIVE_IN_BUILD
        DriveProgram::init();
#endif
    }



    void doResetActions()
    {
        EventClock::stop();

#if CARRT_INCLUDE_PROGDRIVE_IN_BUILD
        DriveProgram::purge();
#endif

        DEBUG_STOP_SERIAL_OUTPUT();

        MemUtils::resetHeap();
    }




    void initializeCPU()
    {
        initSystem();
        initSystemClock();
        initA2D( kA2dReference256V );
    }



    void initializeNetwork()
    {
        I2cMaster::start();
    }



    void initializeDevices()
    {
        // Initialize non-network devices first
        // (gives time for the I2C network to stabilize)
        Battery::initBatteryStatusDisplay();
        Motors::init();

        // Initialize I2C network devices
        Display::init();
        Display::clear();
        Display::displayTopRowP16( sMsgCarrtIs );
        Display::displayBottomRowP16( sMsgInitializing );

        Lidar::init();
        LSM303DLHC::init();
        L3GD20::init();
    }



    void initializeNavigator()
    {
        Display::displayTopRowP16( sMsgCarrtImuIs );
        Display::displayBottomRowP16( sMsgInitializing );

        Navigator::init();
    }

};

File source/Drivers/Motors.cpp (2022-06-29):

/*
    Motors.cpp - Functions for controlling CARRT's drive motors

    Copyright (c) 2022 Igor Mikolic-Torreira.  All right reserved.

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
    You should have received a copy of the GNU General Public License
    along with this program.  If not, see <http://www.gnu.org/licenses/>.
*/




/*
    Inspired by, and had its origins in, the Adafruit library for the Adafruit
    Motor Shield v1, but the code has been heavily modified and specialized for CARRT.
    So much so that the code has practically no resemblance to the Adafruit original, but
    I still wanted to acknowledge the original...
*/




#include "Motors.h"

#include "CarrtPins.h"



// Extend namespace with additional functions and such
namespace Motors
{

    /*
    * The right-rear motor is particularly faster than the other moters,
    * so speed settings for it are adjusted
    */

    uint8_t kRightRearSpeedAdjust   = 12;



    // Bit positions in the 74HCT595 shift register output

    // Rear Right Motor
    const uint8_t kMotor1_A     = 2;
    const uint8_t kMotor1_B     = 3;

    // Front Right Motor
    const uint8_t kMotor2_A     = 1;
    const uint8_t kMotor2_B     = 4;

    // Front Left Motor
    const uint8_t kMotor3_A     = 5;
    const uint8_t kMotor3_B     = 7;

    // Rear Left Motor
    const uint8_t kMotor4_A     = 0;
    const uint8_t kMotor4_B     = 6;


    enum
    {
        kRightRearMotorNbr      = 1,
        kRightFrontMotorNbr     = 2,
        kLeftFrontMotorNbr      = 3,
        kLeftRearMotorNbr       = 4
    };


    uint8_t sLatchState;


    void enable74HCT595();

    void transmitLatch();

    void initMotorPWM();


#if CARRT_TEST_INDIVIDUAL_MOTORS

    void motorCommand( uint8_t motorA, uint8_t motorB, uint8_t cmd );

#endif

};



void Motors::transmitLatch()
{
    setGpioPinLow( pMotorLatchPin );

    setGpioPinLow( pMotorDataPin );

    for ( uint8_t i = 0; i < 8; i++ )
    {
        setGpioPinLow( pMotorClockPin );

        if ( sLatchState & ( 1 << (7-i) ) )
        {
            setGpioPinHigh( pMotorDataPin );
        }
        else
        {
            setGpioPinLow( pMotorDataPin );
        }

        setGpioPinHigh( pMotorClockPin );
    }

    setGpioPinHigh( pMotorLatchPin );
}



void Motors::enable74HCT595()
{
    // Set up the 74HCT595
    setGpioPinModeOutput( pMotorLatchPin );
    setGpioPinModeOutput( pMotorEnablePin );
    setGpioPinModeOutput( pMotorDataPin );
    setGpioPinModeOutput( pMotorClockPin );

    sLatchState = 0;

    // "Reset" the 74HCT595 H-bridge
    transmitLatch();

    // enable the chip outputs!
    setGpioPinLow( pMotorEnablePin );
}



void Motors::initMotorPWM()
{
    // Front Right Motor and Rear Left Motor
    // Use PWM on Arduino pin 5; on Arduino Mega, pin 5 is PE3 (OC3A)
    // Use PWM on Arduino pin 3; on Arduino Mega, pin 3 is PE5 (OC3C)
    // Phase correct PWM, prescale factor 8
    TCCR3A |= ( 1 << COM3A1 ) | ( 1 << COM3C1 ) | ( 1 << WGM30 );   // turn on OC3A and OC3C
    TCCR3B = ( 1 << CS31 );
    OCR3A = 0;
    OCR3C = 0;

    // Front Left Motor
    // Use PWM on Arduino pin 6; on arduino mega, pin 6 is PH3 (OC4A)
    // Phase correct PWM, prescale factor 8
    TCCR4A |= ( 1 << COM4A1 ) | ( 1 << WGM40 );                     // turn on OC4A
    TCCR4B = ( 1 << CS41 );
    OCR4A = 0;

    // Rear Right Motor
    // Use PWM on Arduino pin 11; on arduino mega, pin 11 is PB5 (OC1A)
    // Phase correct PWM, prescale factor 8
    TCCR1A |= ( 1 << COM1A1 ) | ( 1 << WGM10 );                     // turn on OC1A
    TCCR1B = ( 1 << CS11 );
    OCR1A = 0;

    // Set all pins to output mode
    setGpioPinModeOutput( pRearLeftMotorSpeedPin );                 // Pin 05
    setGpioPinModeOutput( pFrontRightMotorSpeedPin );               // Pin 03
    setGpioPinModeOutput( pFrontLeftMotorSpeedPin );                // Pin 06
    setGpioPinModeOutput( pRearRightMotorSpeedPin );                // Pin 11
}



void Motors::setSpeedAllMotors( uint8_t s )
{
    OCR1A = s - kRightRearSpeedAdjust;
    OCR3C = s;
    OCR4A = s;
    OCR3A = s;
}



void Motors::init()
{
    enable74HCT595();

    // Set all motor pins to 0
    sLatchState &= ~_BV( kMotor1_A ) & ~_BV( kMotor1_B )
                & ~_BV( kMotor2_A ) & ~_BV( kMotor2_B )
                & ~_BV( kMotor3_A ) & ~_BV( kMotor3_B )
                & ~_BV( kMotor4_A ) & ~_BV( kMotor4_B );

    transmitLatch();

    initMotorPWM();

    setSpeedAllMotors( Motors::kFullSpeed );
}



void Motors::goForward()
{
    sLatchState |=  _BV( kMotor1_A ) | _BV( kMotor2_A ) | _BV( kMotor3_A ) | _BV( kMotor4_A );
    sLatchState &= ~( _BV( kMotor1_B ) | _BV( kMotor2_B ) | _BV( kMotor3_B ) | _BV( kMotor4_B ) );

    transmitLatch();
}



void Motors::goBackward()
{
    sLatchState &= ~( _BV( kMotor1_A ) | _BV( kMotor2_A ) | _BV( kMotor3_A ) | _BV( kMotor4_A ) );
    sLatchState |=  _BV( kMotor1_B ) | _BV( kMotor2_B ) | _BV( kMotor3_B ) | _BV( kMotor4_B );

    transmitLatch();
}



void Motors::stop()
{
    // A and B both low
    sLatchState &= ~( _BV( kMotor1_A ) | _BV( kMotor1_B )
                | _BV( kMotor2_A ) | _BV( kMotor2_B )
                | _BV( kMotor3_A ) | _BV( kMotor3_B )
                | _BV( kMotor4_A ) | _BV( kMotor4_B ) );

    transmitLatch();
}



void Motors::rotateLeft()
{
    // Right side goes forward
    sLatchState |=  _BV( kMotor1_A ) | _BV( kMotor2_A );
    sLatchState &= ~( _BV( kMotor1_B ) | _BV( kMotor2_B ) );

    // Left side goes backward
    sLatchState &= ~( _BV( kMotor3_A ) | _BV( kMotor4_A ) );
    sLatchState |=  _BV( kMotor3_B ) | _BV( kMotor4_B );

    transmitLatch();
}



void Motors::rotateRight()
{
    // Right side goes backward
    sLatchState &= ~( _BV( kMotor1_A ) | _BV( kMotor2_A ) );
    sLatchState |=  _BV( kMotor1_B ) | _BV( kMotor2_B );

    // Left side goes forward
    sLatchState |=  _BV( kMotor3_A ) | _BV( kMotor4_A );
    sLatchState &= ~( _BV( kMotor3_B ) | _BV( kMotor4_B ) );

    transmitLatch();
}





#if CARRT_TEST_INDIVIDUAL_MOTORS


// cppcheck-suppress unusedFunction
void Motors::setRearRightMotorSpeed( uint8_t s )
{
    // Use PWM on Arduino pin 11; on arduino mega, pin 11 is PB5 (OC1A)
    OCR1A = s - kRightRearSpeedAdjust;
}


// cppcheck-suppress unusedFunction
void Motors::setFrontRightMotorSpeed( uint8_t s )
{
    // Use PWM on Arduino pin 3; on arduino mega, pin 3 is PE5 (OC3C)
    OCR3C = s;
}


// cppcheck-suppress unusedFunction
void Motors::setFrontLeftMotorSpeed( uint8_t s )
{
    // Use PWM on Arduino pin 6; on arduino mega, pin 6 is PH3 (OC4A)
    OCR4A = s;
}


// cppcheck-suppress unusedFunction
void Motors::setRearLeftMotorSpeed( uint8_t s )
{
    // Use PWM on Arduino pin 5; on arduino mega, pin 5 is PE3 (OC3A)
    OCR3A = s;
}


// cppcheck-suppress unusedFunction
void Motors::runRearRightMotor( uint8_t cmd )
{
    motorCommand( kMotor1_A, kMotor1_B, cmd );
}

// cppcheck-suppress unusedFunction
void Motors::runFrontRightMotor( uint8_t cmd )
{
    motorCommand( kMotor2_A, kMotor2_B, cmd );
}
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

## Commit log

2016-10-05 Add schematic of CARRT using Fritzing
    [CARRT.fzz]
2016-11-12 Check-in some of the hardware drivers and test harnesses
2016-11-12 Add driver for gyroscope hardware and test harness
2016-11-13 Add driver for LSM303DLHC Accelerometer/Magnetometer and test harness
2016-11-14 Add master allocation of pins to functions; used by all other code (including drivers)
2016-11-29 Add driver for the wheel motors that drive CARRT around.
2016-11-29 Update pin definitions to include pins used to control the motors
2016-11-29 Add tests for the motor driver
2016-11-29 Include motor drivers in the test build
2016-12-17 Revise the motor tests to make them easier to visually confirm proper rotation of the wheels
2016-12-18 Renamed files with "Rover" in the name to "Carrt" and changed to using "Carrt" lower-case in file and structure naming
2016-12-19 Add driver for LCD display and corresponding test
2016-12-19 Add test for the key pad driver
2016-12-19 Fix typo in Display test driver comments
2016-12-23 Add chords (combinations of buttons) as options
2016-12-23 Renamed some of the chords (button combinations)
2016-12-23 Main code now takes advantage of chords (button combinations)
2016-12-24 Rename CarrtClock to EventClock and make corresponding fix-up
    [CarrtMain.cpp, EventClock.cpp]
2016-12-24 Add LED flash when battery driver initializes
2016-12-24 Fix the order of initialization
    [CarrtMain.cpp]
2016-12-25 Fix up delay() calls and opening comments
    [Beep.cpp]
2016-12-25 Add names for additional two-button chords
2016-12-25 Add acknowledgement of original inspiration and fix comments
    [L3GD20.cpp]
2016-12-25 Rename macro for individual motor testing and fix opening comments
    [Motors.cpp]
2016-12-25 Rename macro fo individual motor testing
2016-12-25 Rename ServoDriver to Servo and make corresponding changes throughout
2016-12-25 Improve names in Servo implementation to make it more self-explanatory
2016-12-25 Add compass, accelerometer, gyroscope, and motor test states for on-board testing
2016-12-25 Make reset process more robust
    [CarrtMain.cpp, MainProcess.cpp]
2016-12-25 Fix start-up battery flash
    [Battery.cpp]
2016-12-25 Add raw and null modes to both accelerometer and gyroscope tests
2016-12-26 Fixed unbalanced brackets in TIMER2 (unused) version
    [EventClock.cpp]
2016-12-26 Re-order and ID test menu items to ease maintenance and make a more compact switch (jump table). Saved 164 btyes simply by making menu IDs sequential.
2016-12-28 Simplify drive programming menus; insert a special prog-finished state at the end of a program run
2016-12-28 Add other programmable drive states (just missing the distance and angle ones)
    [ProgDriveStates.cpp]
2016-12-28 Change the scan so we avoid yield() calls (slew at bottom of one event; read range at top of next event)
    [ProgDriveStates.cpp]
2016-12-29 Switch to better variable names
2016-12-29 Fix the event handler for Scan to trigger on each second instead of each 8th-second
    [ProgDriveStates.cpp]
2016-12-29 Fix the radar drive state to slew correctly
    [ProgDriveStates.cpp]
2016-12-30 Eliminate Motor-related calls in the Pause and Beep programmed drive actions
2016-12-30 Move the servo pin assignment out of the header and into the servo driver implementation (no need for any higher-level code to know the pin assignement)
2016-12-30 Add drive program action (and menu) to rotate CARRT a fixed angle
    [ProgDriveStates.cpp]
2016-12-31 Revise angle rotation state to ensure we don't miss the target heading, or if we overshoot reverse back towards it
    [ProgDriveStates.cpp]
2016-12-31 Correct the calculation of the target heading for rotate-angle action
    [ProgDriveStates.cpp]
2016-12-31 Fix some missing "P16" calls where PROGMEM strings are involved
    [CarrtMain.cpp, ProgDriveStates.cpp]
2016-12-31 Switch the toolchain file
2016-12-31 Revise the reset functionality to provide a 100% reset of the system
    [CarrtMain.cpp]
2017-01-05 Correct filtering for max V
2017-01-06 Make some of the a and v filters easily turned off (for nav experimentation)
2017-01-06 Add programmable actions to drive fixed distances (forward or reverse) based on dead-reckoning (not IMU navigation, at least for now)
    [ProgDriveStates.cpp]
2017-01-07 Minor corrections to gyroscope item
2017-01-12 Ensure motors are turned off as part of a reset
    [MainProcess.cpp]
2017-01-12 Fix typo in comment
    [MainProcess.cpp]
2017-02-22 Fix comment (timer compare, not overflow interrupt that is turned off)
    [EventClock.cpp]
2017-08-20 Ensure conversions of two 1-byte ints to a single 2-byte int are performed correctly
    [L3GD20.cpp, LSM303DLHC.cpp]
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2017-08-21 Lidar code fixes for correct compilation
    [Lidar.cpp]
2017-09-11 Add very basic direct tests of the lidar hardware
2017-09-13 Adjust how to read the lidar to split the read into to separate I2C transactions
2017-09-17 Update basic, low-level testing code for the lidar
2017-09-17 Rename the Lidar driver basic operational test
2017-09-17 Rename the Lidar basic functional test
2017-09-17 Basic Lidar driver functionality implemented
2017-09-18 Add full-up CARRT-mounted Lidar test code, both basic driver testing and full-blown scanning and mapping test.
    [Lidar.cpp]
2017-09-20 Move slewing functionality to the Servo driver, and remove it from the Radar and Lidar drivers
2017-09-20 Rename Radar to Sonar to more correctly reflect the sensor
    [CarrtMain.cpp, ProgDriveStates.cpp, Sonar.cpp]
2017-09-20 Allow selective disabling of either Lidar or Sonar servo functionality
2017-09-20 Enable selective disabling of servo functionality within the Sonar driver
2017-09-22 Incorporate Lidar into the full-up^CARRT test suite
2017-09-22 Add direct servo test code
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2017-09-23 Update Fritzing schematic to reflect the addition of a Lidar
    [CARRT.fzz]
2017-09-23 Update planned drive code to use the lidar; sonar retained for collision avoidance
    [ProgDriveStates.cpp]
2017-09-23 Update the README to reflect the new lidar
2017-09-23 Update readme to reflect lidar and fix broken link to Fritzing in markdown markings
2017-09-24 Add special mode for lidar calibration to the test code
2017-09-24 Refine calibration mode output to streamline importing data into a spreadsheet
2017-09-24 Add (based on testing) warm up pingings when lidar resets
    [Lidar.cpp]
2017-09-24 Lidar warm-up removed from test code--now part of lidar drive init() code
2017-09-24 Add code to adjust lidar ranges based on calibration data
2017-09-25 Tweaking the start-up sequence for lidar ranging test
2017-09-27 LidarRangingTest: replace accidentally delete code to initialize globals and improve outputing of errors in ranging
2017-10-05 Add lidar ping command to return the median of a sample of pings
2017-10-05 Revise lidar map-making test code to use median of sample of lidar pings
2017-10-23 Expand lidar test with path finding option to find a path after building a lidar-based map
2017-10-25 Separate out a path finding test from the lidar ranging test
2017-12-08 Expose a function to access the error state (convenient way to report an error in a function that returns a state)
    [MainProcess.cpp]
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2017-12-10 Capture all cases where memory allocation can fail
    [MainProcess.cpp]
2018-01-14 Add documentation on how current heading is maintained
2018-03-02 Fix missing 'delete this' on various states
    [GotoDriveStates.cpp, ProgDriveStates.cpp]
2018-03-02 Expose interface to immediate change to an error state
    [MainProcess.cpp]
2018-03-03 Clean up Goto drive states code and add shells for the missing classes
    [GotoDriveStates.cpp]
2018-03-04 Clarify Navigator's internal coordinate system and fix incorrect usages
    [GotoDriveStates.cpp]
2018-03-04 Change the sense of how the servo rotates between positive and negative angles
2018-03-11 Adjust individual motor speeds to compensate for motor differences and facilitate straight driving
2018-03-17 Fix white-line spacing between functions
    [GotoDriveStates.cpp]
2018-03-17 Make sure we error if we reach a function we should never reach
    [GotoDriveStates.cpp]
2018-03-21 Update DR parameters after adjusting motor speeds to get a straight drive
2018-11-24 Get rid of the kMinTime 'feature' -- times of zero don't happen and min clock time increment in CARRT is 0.125 seconds in any case. Save code and SRAM.
2018-11-24 Rename 'speed' to 'velocity' in the navigator whenever 2-D velocity is the correct term
2018-11-24 Clean up -- acceleration is ignored and velocity is step-wise constant in DR model of navigation
2018-11-25 Build both IMU and DR version to ensure compiles are tested on both versions
2018-12-02 Fix code in Sonar test and Lidar test
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2018-12-28 Strengthen the crash-avoidance logic when driving in GoTo mode to abort if CARRT can't safely start the drive
    [GotoDriveStates.cpp]
2018-12-28 Revamp debugging to have more consistent macro names and allow easier fine-tuning of what debugging information is sent over serial. CARRT_ENABLE_DEBUG_SERIAL serves as the master debugging ON/OFF sw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
2018-12-29 Start adding a GoTo debug mode that requires hitting the Select button to continue from one step to another. Also begin to fix the mistaken E coordinate to the correct W
    [GotoDriveStates.cpp]
2018-12-29 Add a debugging print function for program space strings
2018-12-30 Fix the conversion from local to global (N, W) coords
    [GotoDriveStates.cpp]
2018-12-30 Fix typos in the comments
    [GotoDriveStates.cpp]
2018-12-31 Minor corrections on comments
    [GotoDriveStates.cpp]
2018-12-31 Fix relative-to-global conversions during scan map-building
    [GotoDriveStates.cpp]
2018-12-31 Fix display of unknown lidar range
    [GotoDriveStates.cpp]
2019-01-01 Fix that first waypoint is origin, so ignore
    [GotoDriveStates.cpp]
2019-01-01 Fix rotating display progress to correct line
    [GotoDriveStates.cpp]
2019-01-01 Fix distance drive and distance computation
    [GotoDriveStates.cpp]
2019-01-01 Fix y-axis labels on debug serial map dump
2019-01-02 Turn to heading now doesn't turn at all if not required. Also switch to using heading from Navigator
    [GotoDriveStates.cpp]
2019-01-06 Clear all map grips between CARRT and lidar obstacle
2019-01-06 Correct computation of relative coords of lidar echo.
    [GotoDriveStates.cpp]
2019-01-06 Fix typo in variable name
    [Motors.cpp]
2023-04-08 Correct comment that outlines process flow logic
    [GotoDriveStates.cpp]
2026-04-02 Fix when debug UART is off.
    [GotoDriveStates.cpp]

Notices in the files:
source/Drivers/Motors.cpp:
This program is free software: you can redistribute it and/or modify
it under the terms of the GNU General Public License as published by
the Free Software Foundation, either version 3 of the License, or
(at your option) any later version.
